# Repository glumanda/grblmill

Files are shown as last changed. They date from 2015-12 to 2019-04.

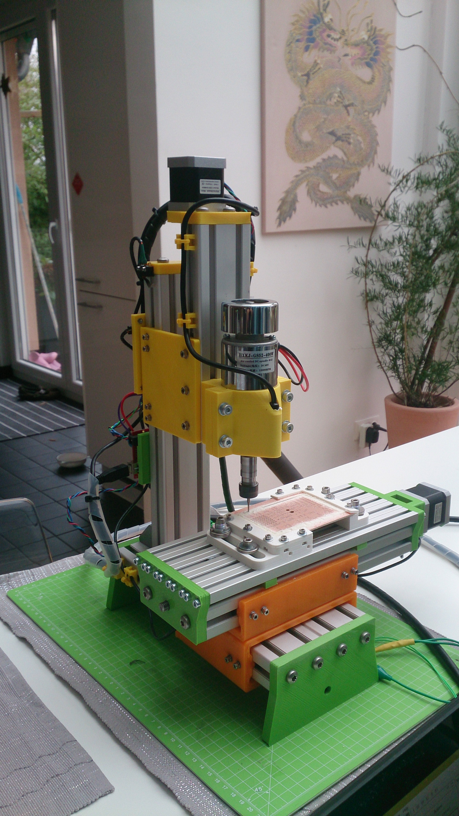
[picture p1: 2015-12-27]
pictures/with_t_plate.JPG

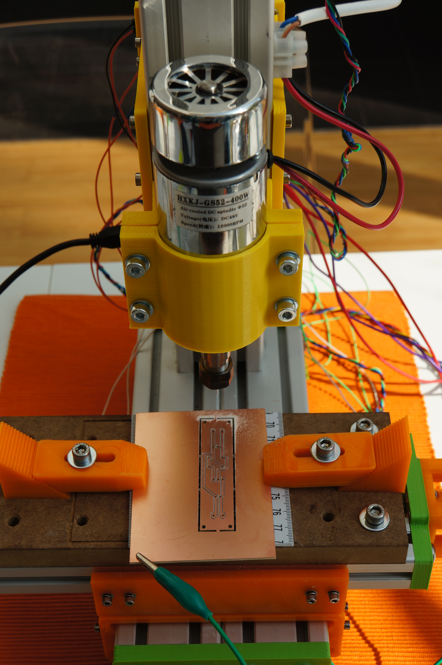
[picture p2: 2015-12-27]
pictures/no_t_plate.JPG

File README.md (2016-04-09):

http://www.thingiverse.com/thing:1228253

##grbl_mill

* fully printable 
  * large parts are printed with a 0.8 mm nozzle
  * smaller parts with a 0.4 mm nozzle
* completly designed with openSCAD
* derived from http://www.thingiverse.com/thing:44854
* you need the MCAD library https://github.com/SolidCode/MCAD

####Usage

* open grbl_mill_main.scad in openSCAD to view the assembled mill
  * you can select the viewed part in the main file by commenting out the appropriate line
* in grbl_mill_const.scad you can adjust the main construction
  * in the division Configuration you can configure the width (count) of profiles for each direction separatly
  * there are some more flags to configuring the mill
* some tuning is done directly in grbl_mill_parts.scad
* all things are downloadable

####Working Area

* xy: 107.5 mm x 84.3 mm
* z = about 40 - 50 mm, depending from tool and using the t-nut profiles
* is enough for milling pcbs or hobbed bolts

####Profiles
* using alu profiles from http://www.kinetikmsystem.de
* K30 for the basic construction
  * you can use for all directions a width of 3 basic profiles (like in the original design)
  * but i had some sourcing restrictions so i am used on y 4 basic profile width and for the other two profiles
  * length for z: 200 mm (movable) and 300 mm (fix)
  * length for x and y: 260 mm
* K20 for the t-nut plate
  * length is the same like for x: 260 mm

####Screws and Rods

* to connect the end parts to the profiles i have used M6 self cutting screws
* to fix the slider and the TR8 nut i used M3 screws
* fixing the t-nut profíles use M4 screws

* the T8 threaded rod and the TR8 nut i have sourced from http://www.metallbau-pietrzak.de (ebay)
* the trapezoid rods are 300 mm (x), 250 mm (y) and 200 m (z) long
* the motor coupler on all axes is from http://www.thingiverse.com/thing:173335

####CNC-Control-Unit and Spindle

* Arduino Uno with Grbl V0.9j https://github.com/grbl/grbl
* GrblShield with DRV8825 driver chips
* the spindle is from ebay (China) with a Driver Board, that can be connected to the Grbl-Board

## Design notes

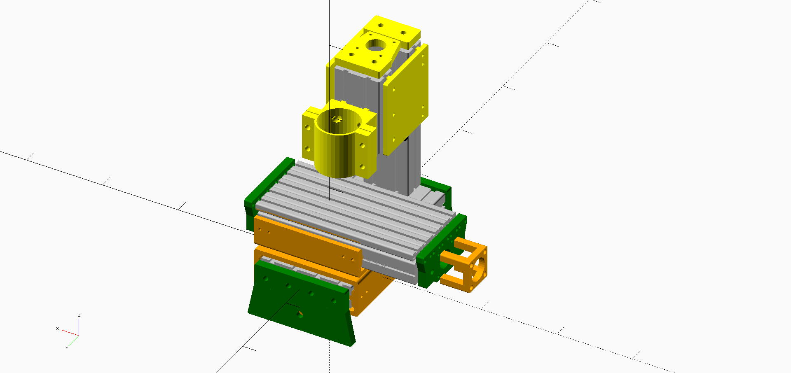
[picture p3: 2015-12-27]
pictures/GrblMill.png

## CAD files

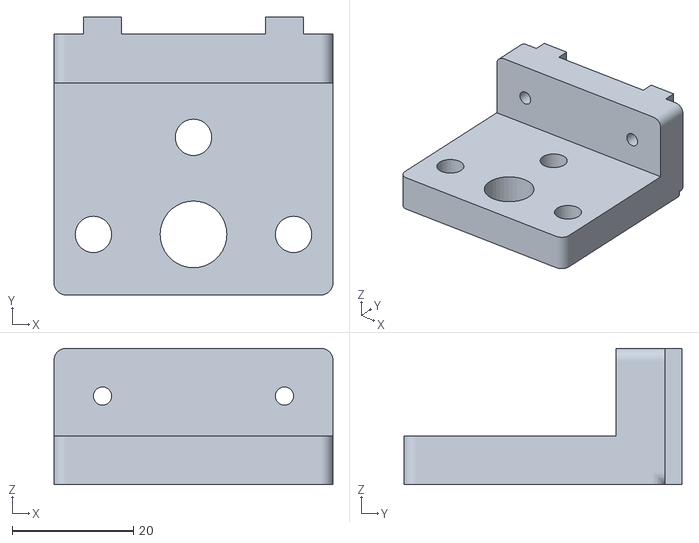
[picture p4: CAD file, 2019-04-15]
things/z_slider_support.stl
46.0 x 45.9 x 22.5

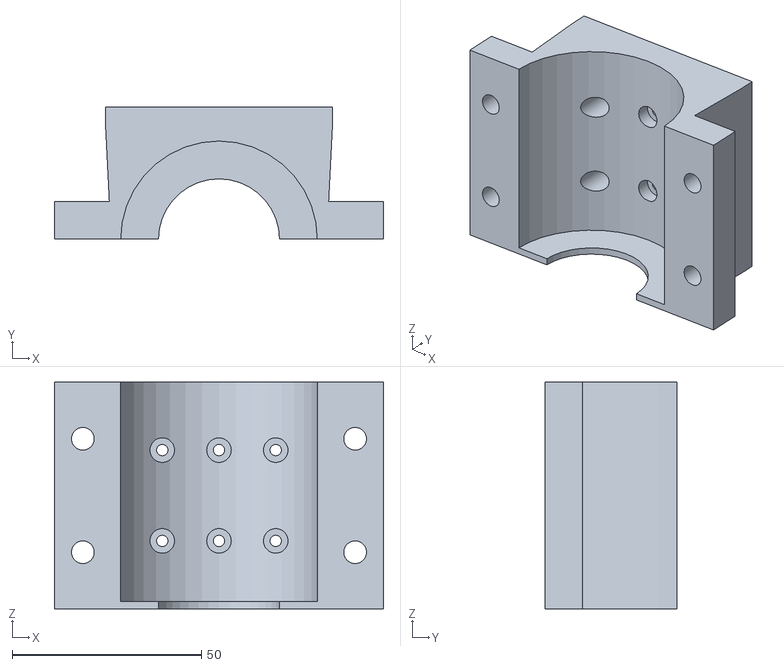
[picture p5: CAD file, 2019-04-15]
things/spindle_base_z-slider.stl
87.0 x 34.9 x 60.0

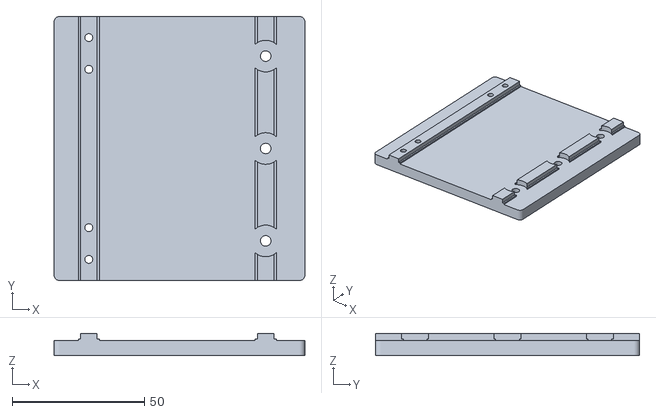
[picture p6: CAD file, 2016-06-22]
things/z_side_slide_v2.stl
95.0 x 100.0 x 8.45

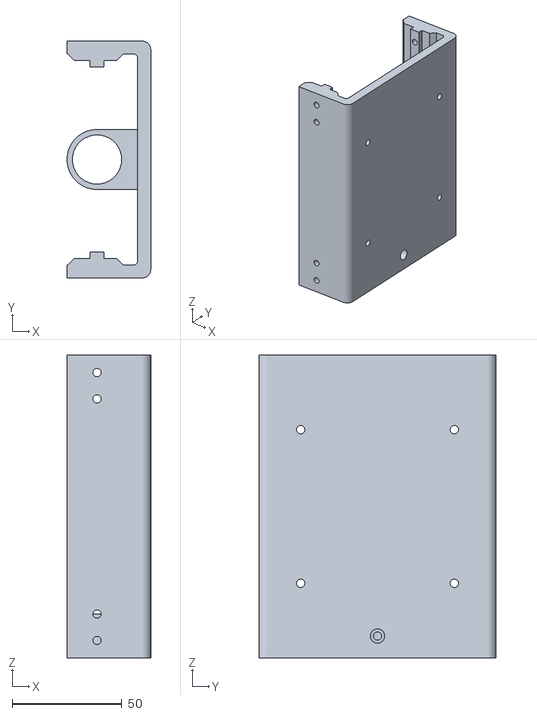
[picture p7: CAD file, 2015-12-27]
things/x_slide.stl
38.1 x 108.0 x 138.0

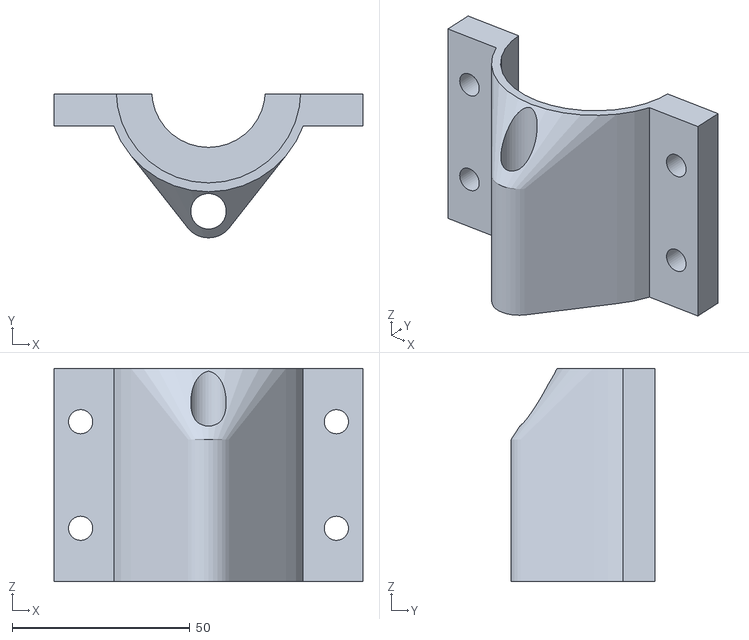
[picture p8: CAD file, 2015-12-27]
things/spindle_clamp_with_cam.stl
87.0 x 40.5 x 60.0

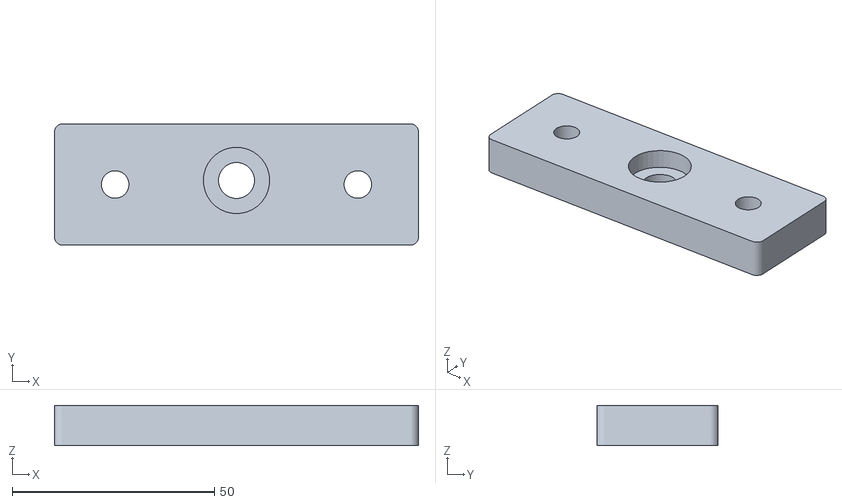
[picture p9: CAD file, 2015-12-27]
things/x_end.stl
90.0 x 30.0 x 10.0

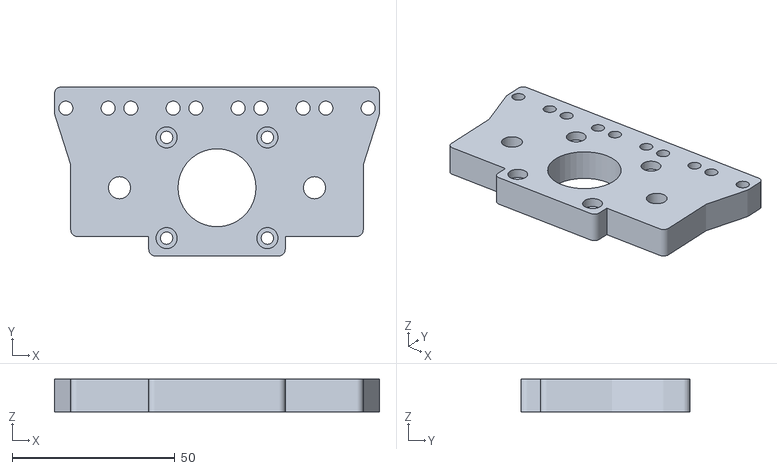
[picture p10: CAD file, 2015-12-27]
things/x_motor_end_with_tplate.stl
100.0 x 52.0 x 10.0

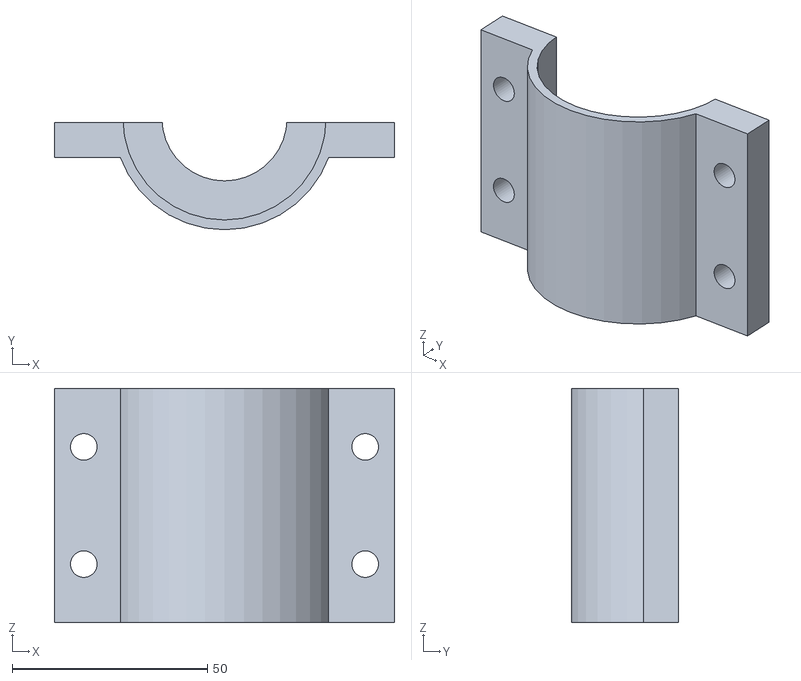
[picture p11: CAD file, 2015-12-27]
things/spindle_clamp_no_cam.stl
87.0 x 27.5 x 60.0

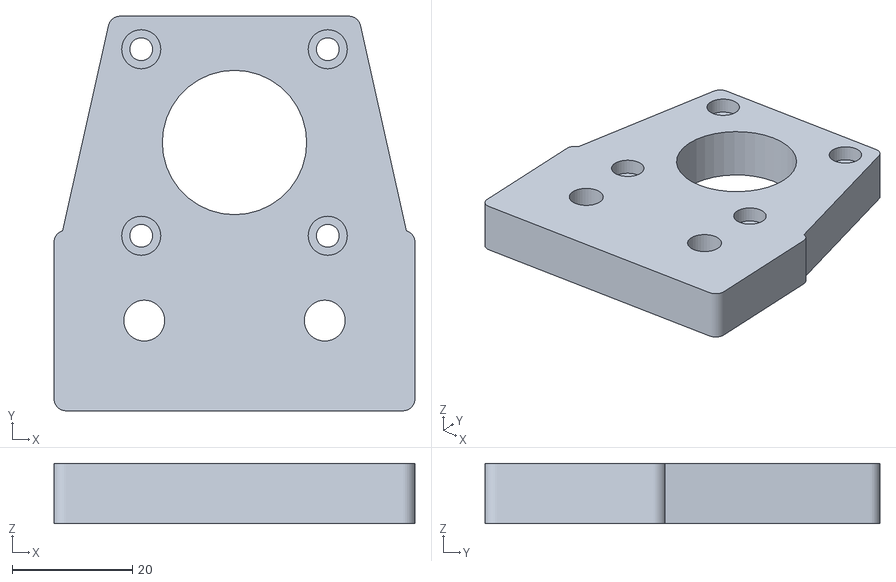
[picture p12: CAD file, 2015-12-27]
things/z_motor_end.stl
60.0 x 65.6 x 10.0

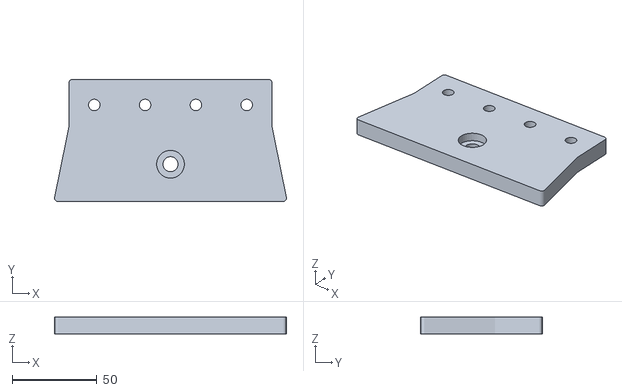
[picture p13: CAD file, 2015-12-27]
things/y_end_support.stl
137.0 x 72.0 x 10.0

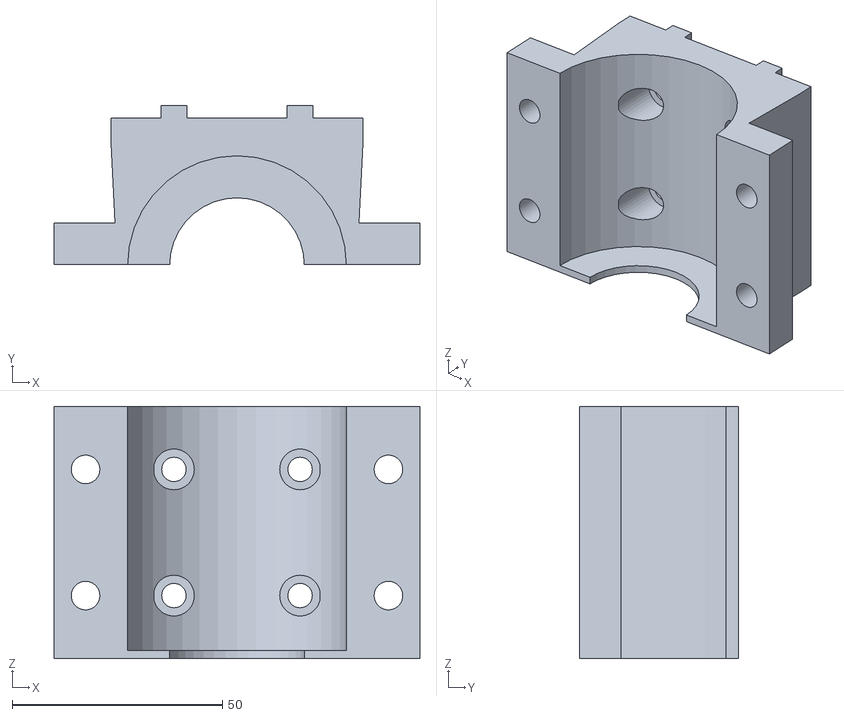
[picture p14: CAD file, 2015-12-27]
things/spindle_base.stl
87.0 x 37.9 x 60.0

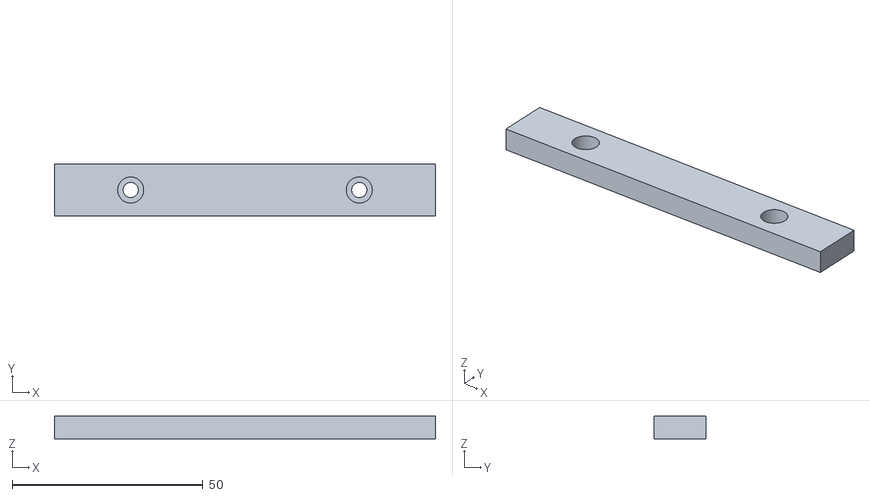
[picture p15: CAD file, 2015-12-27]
things/t_plate_support.stl
100.0 x 13.7 x 6.00

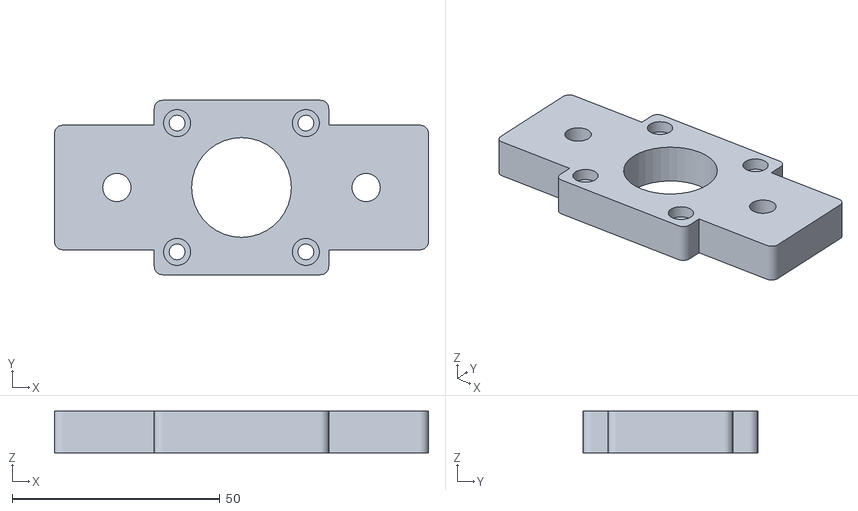
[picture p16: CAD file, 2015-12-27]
things/x_motor_end.stl
90.0 x 42.0 x 10.0

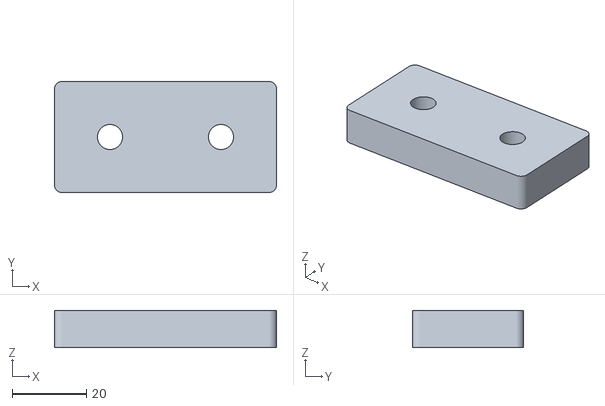
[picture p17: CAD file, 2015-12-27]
things/z_end.stl
60.0 x 30.0 x 10.0

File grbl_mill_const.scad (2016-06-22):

/**
 * junand 30.11.2014
 * last update: 27.12.2015
 *
 * Nachbau der MicroMill-Teile
 * rebuild of the micromill parts
 *
 *      const
 *
 */

/**************************************************************************
 *
 * Basics
 *
 **************************************************************************/

$fn = 360/10;

fudge = 0.1;
fudge_dim = [0, 0, -fudge];

clearance = 0.4;

/**************************************************************************
 *
 * Configuration
 *
 **************************************************************************/

part_height = 10;   // height of all end plates

// number of basic profiles at each axis
x_profile_count = 3;
y_profile_count = 4;
z_profile_count = 2;

spindle_clamp_with_cam_holder = false;
with_t_plate = true;

t_plate_profile_count = 5;

shorter_x_slide = false;

z_nut_base_reduction = 15;
//z_nut_base_reduction = 0;

assemble_show_axes = false; // on for checking alignment

with_z_slider_notch_base = true;
 
/**************************************************************************
 *
 * Index
 *
 **************************************************************************/

//index
outer_diameter = 0; 
inner_diameter = 1;
height = 2;

x = 0;
y = 1;
z = 2;              // identical with height!!! can used synonimously

/**************************************************************************
 *
 * Kinetik Profile
 *
 **************************************************************************/

 // sizes of profiles
profile_k30_base_size = 30;

default_profile_count = 4;

profile3030_k30_end_dim = [profile_k30_base_size, profile_k30_base_size, part_height];
profile6030_k30_end_dim = [2 * profile_k30_base_size, profile_k30_base_size, part_height];
profile9030_k30_end_dim = [3 * profile_k30_base_size, profile_k30_base_size, part_height];
profile12030_k30_end_dim = [4 * profile_k30_base_size, profile_k30_base_size, part_height];

profile_k30_end_dim = [
    [-1, -1, -1],           // placeholder
    profile3030_k30_end_dim,
    profile6030_k30_end_dim,
    profile9030_k30_end_dim,
    profile12030_k30_end_dim
];

// position of profile end holes
profile_end_plate_hole_pos = [profile_k30_base_size/2, profile_k30_base_size/2, 0];

profile_k20_end_dim = [20, 10, part_height];

kinetik_k30_notch_width = 6.40 - 0.10; // according to the drawing this is 6.2 mm, but practical tests result in 6.3 mm
kinetik_k30_notch_depth = 2.85;
kinetik_k30_notch_base_width = 8.00;
kinetik_k30_notch_base_depth = 2.90 - 2.10;

kinetik_k20_notch_width = 5.05;
kinetik_k20_notch_depth = 3;

/**************************************************************************
 *
 * Motor Mount
 *
 **************************************************************************/

nema17_base_size = 42;
nema17_plate_dim = [nema17_base_size, nema17_base_size, part_height];
nema17_axes_cutout_radius = 12;
nema17_base_mounthole_pos = nema17_base_size/2 - 5.5;
nema17_mounthole_pos_dim = [nema17_base_mounthole_pos, nema17_base_mounthole_pos, 0];

x_motor_end_extension_length = 38.5;

/**************************************************************************
 *
 * Screws
 * http://de.wikipedia.org/wiki/Metrisches_ISO-Gewinde
 *
 **************************************************************************/

M3_clearance = 0;
M3_diameter = 3;
M3_radius = M3_diameter/2;
M3_bolthead_radius = 3.25;
M3_bolthead_height = 3;
M3_wrench_size = 5.5;
M3_nut_diameter = M3_wrench_size / sin ( 60 );
M3_nut_radius = M3_nut_diameter/2;
M3_nut_height = 2.3;

M4_clearance = 0;
M4_diameter = 4;
M4_radius = M4_diameter/2;
M4_bolthead_diameter = 6.85;
M4_bolthead_radius = M4_bolthead_diameter/2;
M4_bolthead_height = 3.9;
M4_wrench_size = 7;
M4_nut_diameter = M4_wrench_size / sin ( 60 );
M4_nut_radius = M4_nut_diameter/2;
//M4_nut_height = xx;

M6_clearance = 0;
M6_diameter = 6;
M6_radius = M6_diameter/2;
M6_bolthead_diameter = 9.7;
M6_bolthead_radius = M6_bolthead_diameter/2;
M6_bolthead_height = 6.0;
M6_wrench_size = 10;
M6_nut_diameter = M6_wrench_size / sin ( 60 );
M6_nut_radius = M6_nut_diameter/2;
M6_nut_height = 4.75;

/**************************************************************************
 *
 * TR8 Nuts and Bearings
 *
 **************************************************************************/

TR8_nut = [22 + clearance, -1, 20]; // outer diameter, height
TR8_radius = 8/2;

// outer, inner, height
bearing688_dim = [16 + clearance, 8 + clearance, 5];
bearing688_end_plate_pos = -35;

/**************************************************************************
 *
 * Parts
 *
 **************************************************************************/

corner_radius = 2;
sidesonly = true;

z_nut_base_dim = [26, 31, 12]; // x, y, z

z_side_slide_dim = [95, 100, 5.7]; // x, y, z
z_side_slide_notch_x_pos = [-35.5 -2, +29.5];

inner_slider_short_len = 28;
inner_slider_hole_distance = 12;

z_nut_base_plate_dim = [profile_k30_end_dim [z_profile_count][x], 1.5*profile_k30_base_size, part_height/2];
z_nut_y_pos = -22.5;
z_nut_shell_base_width = TR8_nut [outer_diameter] + 10;
z_nut_fixing_screw_base_width = 10;

TR8_nut_shell_base_height = 2;
TR8_nut_shell_height = TR8_nut [height] + TR8_nut_shell_base_height;
TR8_nut_axes_cutout_diameter = 14;
TR8_nut_shell_width = 2;
// TR8_nut_shell_width = 2.3; // this is better for my slicer

support_cylinder_diameter = 1;

/**************************************************************************
 *
 * Slides
 *
 **************************************************************************/

slide_board_depth = 6; // 6 mm Außenwand
slide_wall_depth = 3; // auf dieser Erhöhung sitzt die Gleitnut
slide_clearance = 0.2;
slide_connector_distance = 35; // distance from midpoint

x_slide_inner_width = profile_k30_end_dim [x_profile_count][x] + 2*slide_wall_depth;
y_slide_inner_width = profile_k30_end_dim [y_profile_count][x] + 2*slide_wall_depth;

x_slide_length = y_slide_inner_width + 2*slide_board_depth;
x_slide_length_cut = 18 + 30;
y_slide_length = x_slide_inner_width + 2*slide_board_depth;

slide_inner_width_extra = 7;

// inner dimension of a slider
// profileX030_end_dim [y] + 2*slide_board_depth + slide_clearance
// 3*30                    + 2*3                         + 0.5 = 96.5 bei 30x90 Profilen

// outer dimension of a slider
// slide_inner_dim [y] + 2*slide_board_depth => 108.5 bei 30x90 Profilen
//          96.5               + 2*      6                  = 108.5

/**************************************************************************
 *
 * Assemble
 *
 **************************************************************************/

assemble_dist = 5;
len_axes = 260;

//----------------------------------------------------------------------------------------------

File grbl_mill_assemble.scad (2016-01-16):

/**
 * junand 08.02.2015
 * last update: 27.12.2015
 *
 * Nachbau der MicroMill-Teile
 * rebuild of the micromill parts
 *
 *      assemble
 *
 */

module assemble_all ( dist = assemble_dist, with_profile = true ) {

    //translate ( [0, -50, -profile_k30_base_size/2] ) 
    rotate ( [90, 0, 0] ) assemble_xy ( dist, with_profile ); 
    //translate ( [0, 120, 50] ) rotate ( [0, 0, 180] ) 
    translate ( [0, -110, profile_k30_base_size/2 + dist] ) rotate ( [0, 0, 180] ) assemble_z ( dist, with_profile, 1.0*z_side_slide_dim [y], 2.0*z_side_slide_dim [y] ); 
    
}

 module assemble_z ( dist = assemble_dist, with_profile = true, z_movable_profile_length = z_side_slide_dim [y], z_fix_profile_length = z_side_slide_dim [y] ) {
 
    // movable profile with spindle clamp
    translate ( [0, -z_side_slide_notch_x_pos [1] - kinetik_k30_notch_width/2, z_fix_profile_length - z_movable_profile_length] ) {
        if ( with_profile ) {
            color ( "silver" ) kinetik_profile_k30 ( z_profile_count, z_movable_profile_length );
        }
        color ( "yellow" ) translate ( [0, 0, z_movable_profile_length + nema17_plate_dim [z] + dist] ) rotate ( [0, 180, 0] ) z_motor_end ();
        color ( "yellow" ) translate ( [0, -profile_k30_base_size/2 -assemble_dist, 0] ) {
            spindle_clamp ( 1 );
            spindle_clamp ( 2 );
        }
    }
    
    // fix profile
    translate ( [0, -z_side_slide_notch_x_pos [0] - kinetik_k30_notch_width/2, 0] ) {
        if ( with_profile ) {
            color ( "silver" ) kinetik_profile_k30 ( z_profile_count, z_fix_profile_length );
        }
        color ( "yellow" ) translate ( [0, 0, z_fix_profile_length + dist] ) z_end ();
        color ( "black" ) translate ( [0, -profile_k30_base_size/2, z_fix_profile_length - z_movable_profile_length -20] ) z_nut ();
    }
    
    // side slides
    color ( "yellow" )
    for ( i = [-1, +1] ) {
        translate ( [i*(z_profile_count*profile_k30_base_size/2 + z_side_slide_dim [z]/2 + dist), 0, z_side_slide_dim [y]/2 + z_fix_profile_length - z_movable_profile_length] ) 
            rotate ( [i*90, 0, -90] ) 
                z_side_slide ();
    }
    
    // z axes
    if ( assemble_show_axes ) {
        color ( "red" )
            translate ( [0, -3, -25] )
                rotate ( [0, 0, 0] )
                    cylinder ( d = 8, h = len_axes );
    }
    
 }

module assemble_y ( dist = assemble_dist, with_profile = true, y_profile_length = y_slide_length ) {
 
    // y slider
    union () {
        color ( "green" ) y_end_support ();    
        translate ( [0, 0, part_height + dist] ) {
            if ( with_profile ) {
                color ( "silver" ) translate ( 2*fudge_dim ) kinetik_profile_k30 ( y_profile_count, y_profile_length +4*fudge );
            }
            color ( "orange" ) rotate ( [0, 0, 90] ) y_slide ();
            translate ( [0, 0, y_profile_length + dist + part_height] ) {
                color ( "green" ) rotate ( [0, 180, 0] ) y_motor_end_support ();
            }
        }
    }

}

module assemble_x ( dist = assemble_dist, with_profile = true, x_profile_length = x_slide_length ) {

    // x slider
    union () {
        color ( "green" ) rotate ( [180, 180, 0] ) x_end ();
            translate ( [0, 0, part_height + dist] ) {
                color ( "silver" )
                if ( with_profile ) {
                    for ( d = [-1, +1] ) {
                        translate ( [d*(x_profile_count-1)/2*profile_k30_base_size, 0, -2*fudge] ) kinetik_profile_k30 ( 1, x_profile_length +4*fudge );
                    }
                    if ( with_t_plate ) {
                        for ( i = [1 : t_plate_profile_count] ) {
                            translate ( [(0.5 + t_plate_profile_count/2 - i) * profile_k20_end_dim [x], -(nema17_base_size + profile_k20_end_dim[y])/2], 0 ) rotate ( [0, 0, 180] ) kinetik_profile_k20 ( 1, x_profile_length +4*fudge );
                        }
                    }
                }
            color ( "orange" ) rotate ( [0, 0, 90] ) x_slide ();
            translate ( [0, 0, x_profile_length + dist] ) {
                color ( "green" ) translate ( [0, 0, part_height] ) rotate ( [180, 0, 0] ) x_motor_end ();
                translate ( [0, 0, part_height + dist] ) {
                    color ( "orange" ) x_motor_end_extension ();
                }
            }
        }
    }
 
}

module assemble_xy ( dist = assemble_dist, with_profile = true, x_profile_length = 1.5*x_slide_length, y_profile_length = 2.0*y_slide_length ) {

    x_slide_move_x = part_height + dist + x_slide_length/2;
    x_slide_move_y = profile_k30_base_size + slide_inner_width_extra + 2*slide_board_depth + dist;

    y_slide_move = part_height + dist + y_slide_length/2;

    translate ( [x_slide_move_x, x_slide_move_y, 0] ) rotate ( [0, 90, 180] ) assemble_x ( dist, with_profile, x_profile_length );
    translate ( [0, 0, -y_slide_move] ) assemble_y ( dist, with_profile, y_profile_length );
    
}

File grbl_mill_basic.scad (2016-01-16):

/**
 * junand 08.02.2015
 * last update: 27.12.2015
 *
 * Nachbau der MicroMill-Teile
 * rebuild of the micromill parts
 *
 *      basic
 *
 */

 /**************************************************************************
 *
 * Helper
 *
 **************************************************************************/

 module lineup ( space = 40 ) {
 
   for ( i = [0 : $children - 1] )
     translate ( [0, i * space, 0 ] ) children ( i );
     
 }
 
 
module cubedBox ( dim ) {

    translate ( [-dim[0]/2, -dim[1]/2, 0] ) cube ( dim );
    
}

module roundedBox2 ( dim, corner_radius, sidesonly ) {

    translate ( [0, 0, dim [2]/2] ) roundedBox ( dim, corner_radius, sidesonly );
    
}
 /**************************************************************************
 *
 * Kinetik Profile K20
 *
 **************************************************************************/

module kinetik_slot_k20 ( l = 100 ) {

    translate ( [-kinetik_k20_notch_width/2, -kinetik_k20_notch_depth/2, 0] ) cube ( [kinetik_k20_notch_width, kinetik_k20_notch_depth, l] );
    
}

module kinetik_profile_k20 ( count = 2, l = 100 ) {

    dim = [profile_k20_end_dim[x], profile_k20_end_dim[y], l];
    
    translate ( [+dim[x]/2 * (1 - count) , 0, 0] )
        for ( i = [0:count-1] ) {
            translate ( [i*dim[x], 0, 0] ) {
                difference () {
                    roundedBox2 ( dim, corner_radius, sidesonly );
                    translate ( [0, +dim[y]/2 - kinetik_k20_notch_depth/2 +fudge, -fudge] )kinetik_slot_k20 ( l +2*fudge );
                    for ( dx = [-1, +1] ) {
                        translate ( [dx*13/2, -1.5, -fudge] ) cylinder ( d = 3.3, h = l +2*fudge );
                    }
                }
            }
        }
    
}

module kinetik_profile_end_plate_k20_holes ( count = 1, plate_height = profile_k20_end_dim[height] ) {

    hole_diameter = 4.3;
    dim = profile_k20_end_dim;

    translate ( [+dim[x]/2 * (1 - count) , 0, 0] )
        for ( i = [0:count-1] ) {
            translate ( [i*dim[x], 0, 0] )
                for ( dx = [-1, +1] ) {
                    translate ( [dx*13/2, -1.5, -fudge] ) cylinder ( d = hole_diameter, h = plate_height +2*fudge );
                }
        }

}

module kinetik_profile_end_plate_k20 ( count = 1 ) {

    dim = profile_k20_end_dim;
    
	h = dim [height];
	dim_xy = [count*dim [x], dim [y], dim[y]];

    difference () {
        roundedBox2 ( dim_xy, corner_radius, sidesonly );
        kinetik_profile_end_plate_k20_holes ( count );
    }

}

/**************************************************************************
 *
 * Kinetik Profile K30
 *
 **************************************************************************/

module kinetik_slot_k30 ( l = 100 ) {

    color ( "lime" )
    translate ( [-kinetik_k30_notch_width/2, -kinetik_k30_notch_depth/2, 0] ) cube ( [kinetik_k30_notch_width, kinetik_k30_notch_depth, l] );
    
}

module kinetik_profile_k30 ( count = 2, l = 100 ) {

    _dim = profile_k30_end_dim [ count ];
    dim = [_dim[x], _dim[y], l];
    
    difference () {
        color ( "blue" ) roundedBox2 ( dim, corner_radius, sidesonly );
        
        for ( dx = [-1, +1] ) {
            translate ( [dx*(dim[x]/2-kinetik_k30_notch_depth/2+fudge/10), 0, -fudge] ) rotate ( [0, 0, 90] ) kinetik_slot_k30 ( l +2*fudge );
        }
        
        for ( i = [0 : (count/2-(1-count%2))] ) {
            for ( dx = [-1, +1] ) {
                translate ( [dx*(i+0.5*(1-count%2))*profile_k30_base_size, 0, 0] ) {
                    translate ( [0, 0, -fudge] ) cylinder ( r = M6_radius, h = l +2*fudge );
                    for ( dy = [-1, +1] ) {
                        translate ( [0, dy*(profile_k30_base_size/2-kinetik_k30_notch_depth/2+fudge/10), -fudge] ) rotate ( [0, 0, 0] ) kinetik_slot_k30 ( l +2*fudge );
                    }
                }
            }
        }
        
    }
    
}

module kinetik_profile_end_plate_k30 ( count = 0, mid_hole = false ) {

    dim = profile_k30_end_dim [ count ];
    
	h = dim [height];
	dim_xy = [dim [x], dim [y], 0];

	difference ()  {

		translate ( [0, 0, h/2] )
			roundedBox ( dim, corner_radius, sidesonly );
	
		// M6 left/right
        for ( i = [-1, +1] ) {
            translate ( i * (dim_xy/2 - profile_end_plate_hole_pos) + fudge_dim ) 
                cylinder ( r = M6_radius, h = h + 2*fudge );
        }
	
		// M6 mid
        // TODO
		if ( mid_hole ) {
            // there are only mid holes for count 3 and 4
            if ( count == 3 ) {
                // one extra hole at (0,0)
                translate ( [0, 0, -fudge] ) 
                    cylinder ( r = M6_radius, h = h + 2*fudge );
            }
            else if ( count == 4 ) {
                for ( i = [-1, +1] ) {
                    translate ( [i * profile_end_plate_hole_pos [x], 0, -fudge] ) 
                        cylinder ( r = M6_radius, h = h + 2*fudge );
                }
            }
            
		}

	}

}

 /**************************************************************************
 *
 * Nema 17
 *
 **************************************************************************/

module nema17_mount_plate ( h = nema17_plate_dim [height] ) {

    dim = [nema17_plate_dim [x], nema17_plate_dim [y], h];

    translate ( [0, 0, h/2] )
        roundedBox ( dim, corner_radius, sidesonly );
    
}

module nema17_mount_holes ( h = nema17_plate_dim [height], cutout_radius = nema17_axes_cutout_radius ) {

    // motor axes
    translate ( fudge_dim ) cylinder ( r = cutout_radius, h = h + 2*fudge );
    
    // motor mount
    for ( xx = [-1, 1] ) {
        for ( yy = [-1, 1] ) {
            translate ( [xx * nema17_mounthole_pos_dim [0], yy * nema17_mounthole_pos_dim [1], 0] ) {
                translate ( fudge_dim )
                    cylinder ( r = M3_radius, h = h + 2*fudge );
                translate ( [0, 0, h - M3_bolthead_height] ) 
                    cylinder ( r = M3_bolthead_radius, h = M3_bolthead_height + fudge );
            }
        }
    }

}

 /**************************************************************************
 *
 * Bearing
 *
 **************************************************************************/

module bearing688 () {

    // bearing outer dim 16 mm
    translate ( [0, 0, part_height - bearing688_dim [height]] ) // TODO bad reference X030
        cylinder ( r = bearing688_dim [outer_diameter]/2, h = bearing688_dim [height] + fudge );
    // bearing inner dim 8 mm
    translate ( fudge_dim ) 
        cylinder ( r = bearing688_dim [inner_diameter]/2 + 0.25, h = bearing688_dim [height] + 2*fudge );

}

 /**************************************************************************
 *
 * Slider
 *
 **************************************************************************/

module slide_frame ( inner_width, length, length_cut = 0 ) {

    inner_dim = [profile_k30_base_size + slide_inner_width_extra, inner_width + slide_clearance, length - length_cut +2*fudge];
    outer_dim = [inner_dim [x] + 2*slide_board_depth, inner_width + 2*slide_board_depth, length - length_cut];
    
    //echo ( "slide_dim=", outer_dim );

    difference () {
    
        union () {

            difference () {
                translate ( [0, 0, length/2] ) roundedBox ( outer_dim, 2*corner_radius, sidesonly );
                translate ( [0, 0, length/2] ) roundedBox ( inner_dim, corner_radius, sidesonly );
            }

            // Auswölbungen innen für die Nut
            for ( dir = [-1, 1] ) {
                translate ( [0, dir * inner_dim [y]/2, length_cut/2] )
                    mirror ( [0, dir == 1 ? 1 : 0, 0] ) {
                        // Auswölbung
                        linear_extrude ( height = length - length_cut) {
                            polygon (
                                points = [ [12,0], [9,slide_wall_depth], [-10.5,slide_wall_depth], [-13.5, 0] ],
                                paths = [ [0, 1, 2, 3] ]
                            );
                        }
                        // Nut
                        translate ( [-kinetik_k30_notch_width/2, 3 -fudge, 0] ) cube ( [kinetik_k30_notch_width, kinetik_k30_notch_depth, length - length_cut] );
                    }
            }
            
        }
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

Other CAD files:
things/y_slide.stl
things/y_motor_end_support.stl
things/x_end_with_tplate.stl
things/x_motor_end_extension.stl
grbl_mill_innerslider.scad
grbl_mill_main.scad
grbl_mill_parts.scad
things/inner_slider.stl
things/z_nut.stl
things/z_nut_v2.stl
things/z_side_slide.stl

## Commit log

2015-12-27 Initial commit for grbl mill
    it uses MCAD https://github.com/SolidCode/MCAD
    [grbl_mill_assemble.scad, grbl_mill_basic.scad, grbl_mill_const.scad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]
2015-12-27 changed picture for hobbed bolt
2015-12-27 all things generated as stl
    [inner_slider.stl, spindle_base.stl, spindle_clamp_no_cam.stl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]
2015-12-27 Refinements before publishing to thingiverse
    [grbl_mill_assemble.scad, grbl_mill_const.scad, grbl_mill_main.scad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]
2015-12-27 added link to grbl
2015-12-27 Fixed wrong positioning of nut-covering to lowest position.
    [grbl_mill_parts.scad, x_slide.stl]
2016-01-01 Improvements and Code Refactorings for z-Nut
    [grbl_mill_const.scad, grbl_mill_parts.scad, z_nut_v2.stl]
2016-01-16 Better z_nut
    - some refactorings and renamings
    [grbl_mill_assemble.scad, grbl_mill_basic.scad, grbl_mill_const.scad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]
2016-02-19 Improved z_side_slide
    sliding notch more adapted to profiles
    [grbl_mill_const.scad, grbl_mill_parts.scad, z_side_slide_v2.stl]
2016-04-09 Some Fixing for z_side_slider
    [grbl_mill_const.scad, grbl_mill_parts.scad]
2016-06-22 Calculations motorsteps and speedsadded
    [Stepper Motor Resolution.xlsx]
2016-06-22 More Fixings for z_side_slider
    [grbl_mill_const.scad, z_side_slide_v2.stl]
2016-06-25 Fixing Calculations
    calculation of max speed corrected
    [Stepper Motor Resolution.xlsx]
2019-04-12 motor resolution changed to 0.9°
    - before was 1.8°
    [Stepper Motor Resolution.xlsx]
2019-04-15 reworks for new z-axis
    [grbl_mill_main.scad, grbl_mill_parts.scad, spindle_base_z-slider.stl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]
2019-06-02 added module psoc_board_holder
    [grbl_mill_main.scad, grbl_mill_parts.scad]
